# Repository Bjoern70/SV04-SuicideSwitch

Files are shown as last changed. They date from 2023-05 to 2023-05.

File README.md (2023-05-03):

# SUICIDE SWITCH FOR SOVOL SV04 IDEX 3D-PRINTER

## Specification:

### Requirements:

 - Add functionality to power off SV04 printer automatically after finishing print.
 - Safe electrical relization with minimum changes on existing high voltage connections.
 - Low power consumption of additional electronic components iot ensure motherboard / printer stability.
 - Maximum cost below 50 EUR / US-$

### Hardware approach:

 - Use solid state relais (SSR) to switch high voltage phase connection of power supply unit (PSU).
 - Avoid separate high voltage switching outside of SSR. Use low power push-button & separate 9V battery instead.
 - Build separate power-on panel to start printer. Use LEDs to visualize when SSR is powered by Battery and/or PSU.
 - Fix power-on panel to printer structure outside of printer cabinet.
 - Minimize number of & electronic components inside power-on panel.
 - Electronic components inside cabinet have to be fixed casing without impact on cooling & minimum impact on existing components.
 - Use 24V DC to power SSR when printer has started. Limit current to minimize power consumption & SSR input.
 - Use darlington transistor to minimize current consumption from J2 connector.

### Software approach:
 - Utilize spare J2 connector on v5.2.1 motherboard as suicide pin:
 - Add pin definition to motherboard "pins_CREALITY_V4.h" / "pins_CREALITY_V521.h" file: 
  ```//
  // SuicidePin
  //
  #define SUICIDE_PIN PE4 // Connector J2
  #ifndef SUICIDE_PIN_STATE
    	#define SUICIDE_PIN_STATE LOW
  #endif
  Reconfigure Marlin firmware "configuration.h" file iot use M81 g-code command (Power Off):
  // Custom Power Supply Control
  //
  #define HAS_SUICIDE_PIN
  //
  ```
- Add enable/disable auto power-off function to print options display screen.
- Add global bool variable to file "LCD_RTS.h" representing auto power-off enabled/disabled state. Add icons representing state to file "41_control.icl".
- Add AUTO_POWER_OFF_ICON_VP address definition to file "LCD_RTS.h". Add menu item to change state to adjustment phase in 32_main.icl.
- Add handling routine for state change to file "LCD_RTS.cpp" Add state check to suicide() function in MarlinCore implementation.
 
# Operating instructions:

## Power on printer:

- Switch on printer power switch => printer stays powered off. 

- Press push button on panel => yellow LED lights up. 

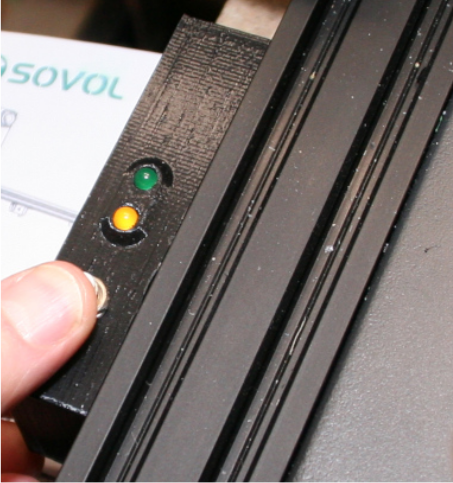
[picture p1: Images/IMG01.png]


- Hold button until green LED lights up.

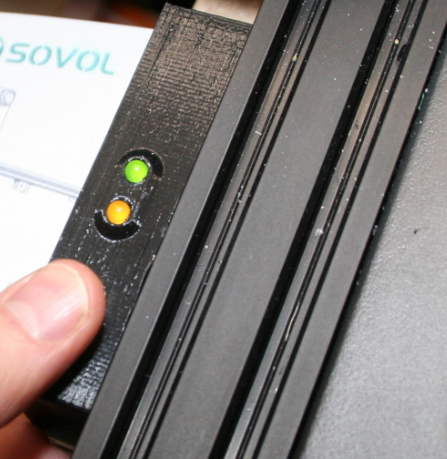
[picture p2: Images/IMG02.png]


- Release button => printer stays powered on.

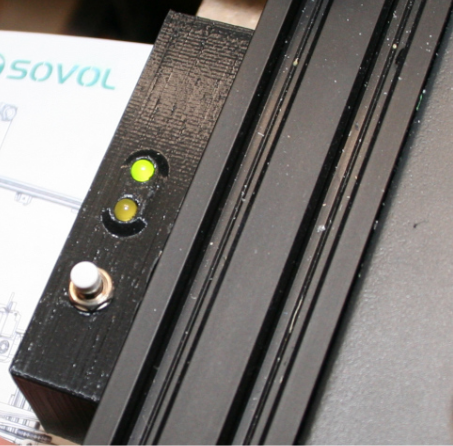
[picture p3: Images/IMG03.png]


## Turn off printer: 

- Option A: Use power switch to turn off.

- Option B: Use power off function in settings menu.

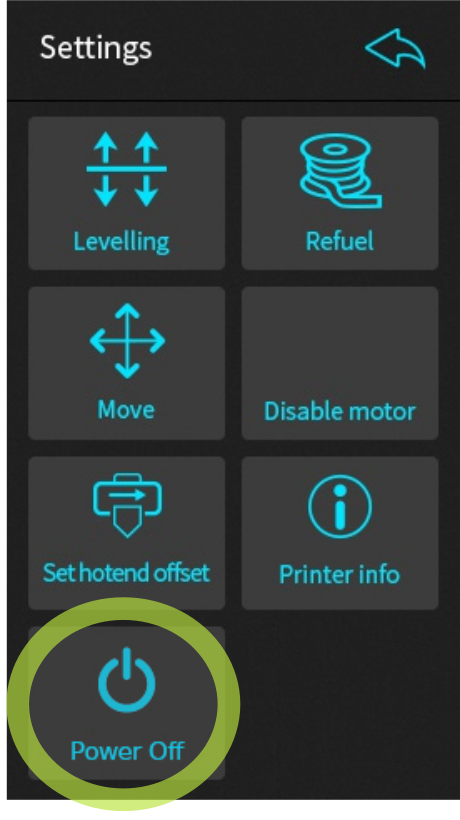
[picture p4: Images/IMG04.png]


- Option C: Add M81 gcode command to custom slicer end gcode. Printer will turn off when executing this instruction. 
   ```
   ; Example for prusa-slicer:
   ; nozzle cool-down & power off command
   M84 ; disable motors
   M104 S0 T0 ; turn off nozzle 0 temperature
   M104 S0 T1 ; turn off nozzle 1 temperature
   M140 S0 ; turn off bed
   M106 P0 ; fan max power iot prevent dropping of filament
   M109 S90 T0 ; wait for nozzle 0 cooldown
   M109 S90 T1 ; wait for nozzle 1 cooldown
   M81 ; suicide
   ```
# Build instructions:

## Important note: 	Changing your printer hardware might void your warranty. Follow this instructions on your own risk & liability.

## List of parts (maybe some components seem over-powered, but I had them available):
- solid state relais type SSR DA-20 
- NPN darlington transistor BDX53C
- Mini push button 0.3A, normally open, 7.2mm (9/32") mounting hole
- LED green, 5mm, 20mA
- LED yellow, 5mm, 20mA
- resistor 10KΩ, 0.25W
- resistor 1KΩ, 0.25W
- resistor 470Ω, 0.25W
- 9V block battery
- 9V battery snap
- cable grommet, 6mm diameter
- 10-20x cable zip tie
- 2x forked cable lug, 1.5-2.5mm², hole diameter M5
- 2m wire yellow+brown+red
- heat shrink tube 4mm diameter
- JST XH 2.54 3-Pin female connector
- 2x socket / button head screw M4x20mm + hex nut
- flat / countersunk screw M3x8mm + washer + hex nut
- 4x socket cap head screw M4x20mm + M4 T-slot nut

## Optional parts to support inside cabinet installation:
- SV04_Side_Supports.stl derived from: https://www.thingiverse.com/thing:5674611
- 3x socket / button head screw M4x10mm + washer + M4 T-slot nut

## Circuit diagram:

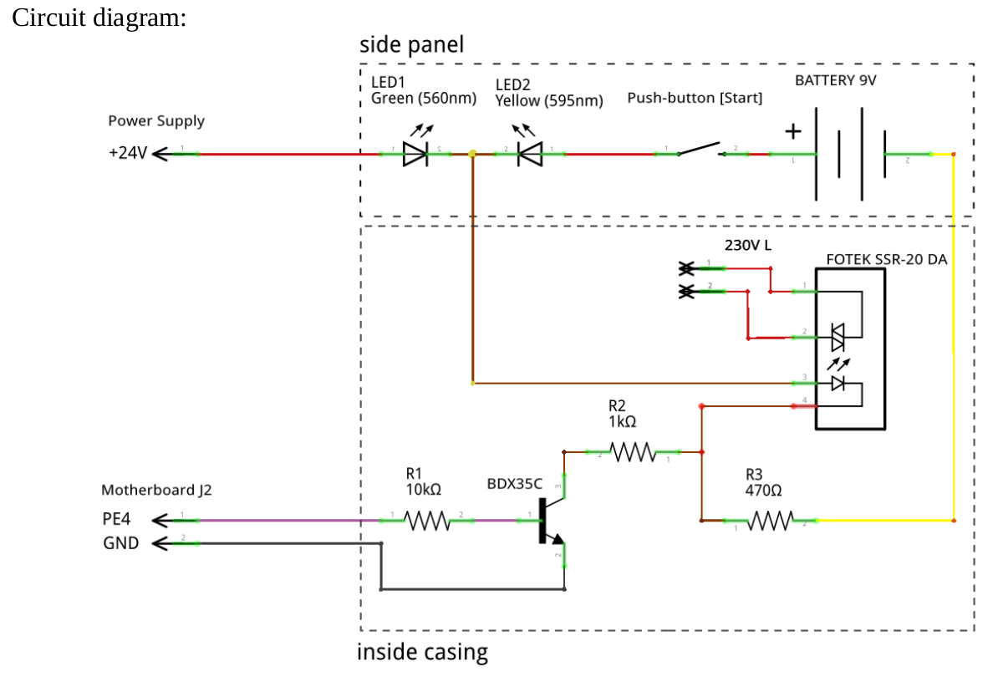
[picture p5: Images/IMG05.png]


## Build side panel:
- Print side panel file "SidePanel.stl".
- Minimum cable length is 60cm/24inch. 3 wires (red, brown, yellow) are needed. 
- Insert yellow LED next to push button opening. Insert green LED. Ensure that LED cathodes point to each other. Bend, cut & solder both LED cathodes with brown cable.
- Bend, cut & solder green LED anode with red cable. Use shrink tube to insulate.
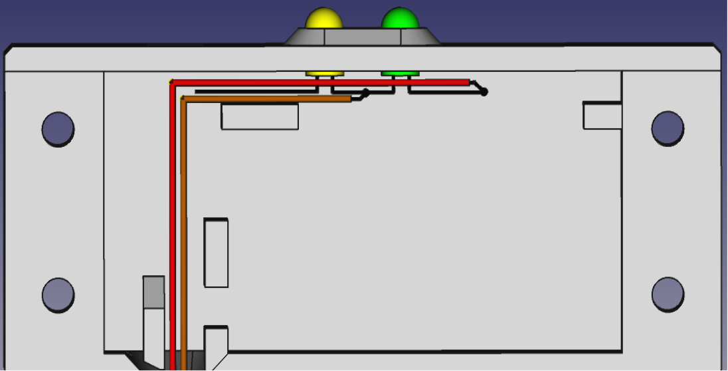
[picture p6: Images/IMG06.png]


- Insert & fasten mini push button. Bend, cut & solder yellow LED anode with mini push button contact. Attach other mini push button contact to positive/red battery snap wire & solder. 
- Connect negative/black battery snap wire to yellow cable & solder. Use shrink tube to insulate.
- Add cable tie for strain relief or just wrap cable around post as pictured. 
- Attach 9V battery to battery snap & insert into side panel. 
- Insert four M4x20mm screws & attach M4 T-slot nuts.

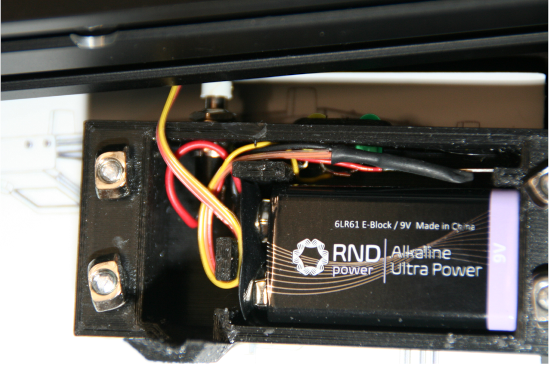
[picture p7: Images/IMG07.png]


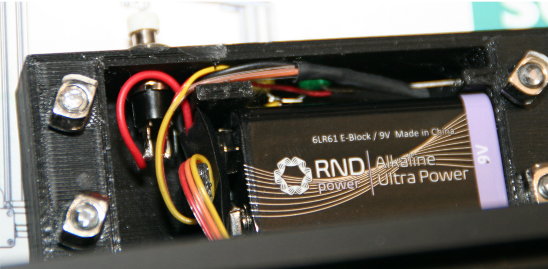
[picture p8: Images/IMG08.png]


## Cabinet preparation:

### IMPORTANT SAFETY NOTE: Unplug power cord first.
- Mark SSR drill holes on top of the cabinet.

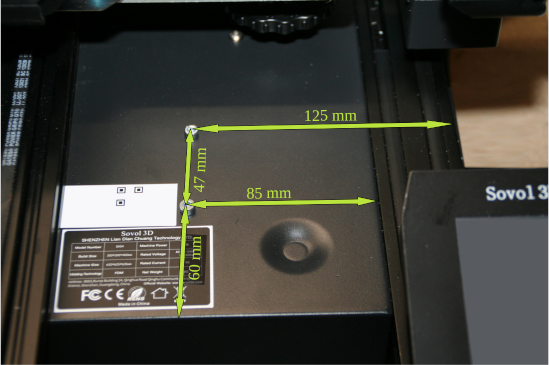
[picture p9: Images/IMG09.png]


- Install optional side supports, lay down printer on its right side.

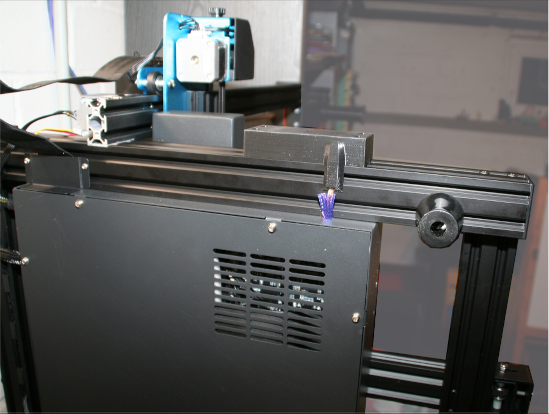
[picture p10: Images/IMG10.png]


- Remove bottom plate screws.
- Cover inside of drilling area with a strip of duct tape iot catch all metal drilling chips & a piece of wooden board iot avoid damage to motherboard / ribbon cable in case of accidently drilling too deep. Carefully drill 6mm hole into left side of cabinet.

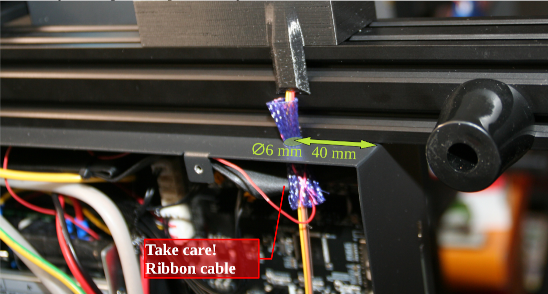
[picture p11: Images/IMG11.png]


- Cover inside of drilling area with a strip of duct tape iot catch all metal drilling chips. Carefully drill two 4,5 mm SSR holes into top side of cabinet. Ensure that holes match SSR fasteners & that sufficent space is left to mount & connect the SSR.

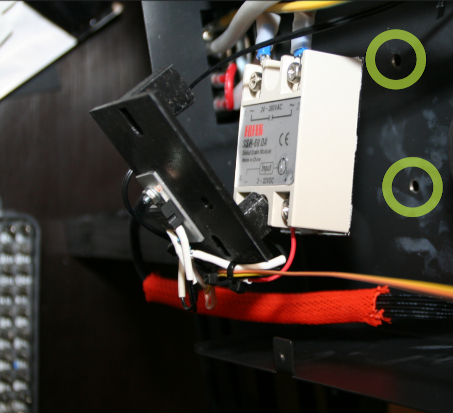
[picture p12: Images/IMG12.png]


- Insert cable grommet into 6mm hole. Mount side panel, pull side panel cable through cable grommet.

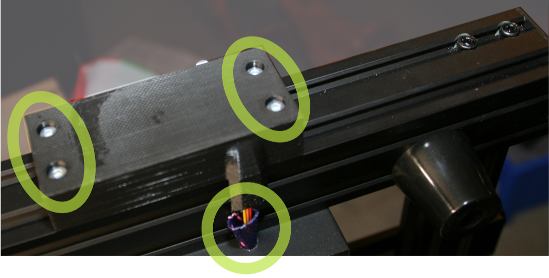
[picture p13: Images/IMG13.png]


- Prepare mainboard JST connector:
- Minimum cable length is 40cm/16inch. Only 2 wires (PE4 + GND) are needed. 

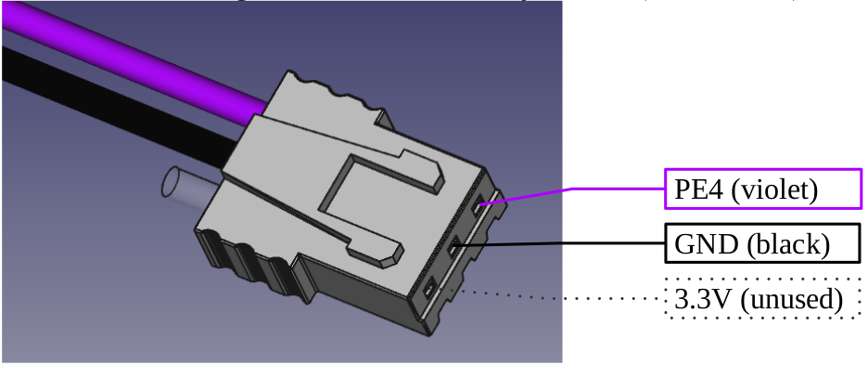
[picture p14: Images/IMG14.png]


##Build inside cabinet unit:
- This design does not use a circuit board. All electronic parts will be attached to the SSR/SSR cover. 
- Print SSR cover file "SSR_cover.stl".
- Insert M3x8mm screw into countersunk hole.

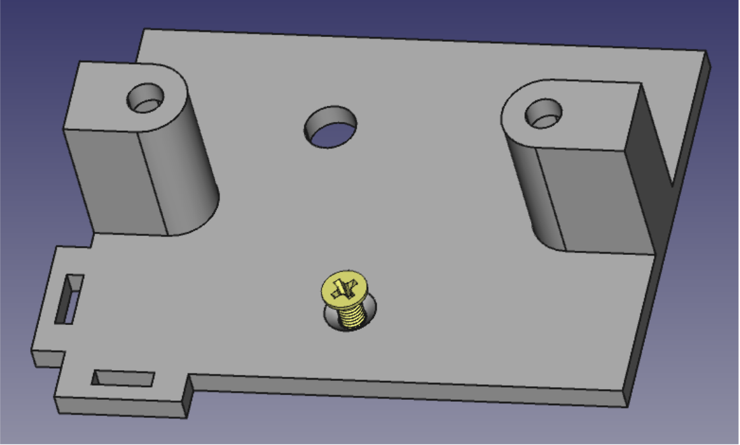
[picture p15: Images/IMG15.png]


- Fix transistor (& optional cooling plate) to M3x8 screw using hex nut & washer.

- Put 40mm shrink tube on JST connector violet cable (PE4). Cut & solder 10KΩ resistor to transistor base (bottom pin). Cut & solder other resistor end to JST connector violet cable (PE4). Shrink tube to insulate transistor pin & resistor.
- Cut & solder 1KΩ resistor to transistor collector (middle pin). Cut & solder other 1KΩ resistor end to 470Ω resistor & 10cm red wire (will be attached to SSR terminal 4). Put 40mm shrink tube on yellow side panel cable. Cut & solder other 470Ω resistor end to yellow side panel cable. Shrink tube to insulate 470Ω resistor.
- Use shrink tube to insulate red SSR wire next to 1KΩ resistor. Fasten red SSR wire to SSR terminal 4 (-).
- Put 40mm shrink tube on JST connector black cable (GND). Cut & solder transistor base (top pin) to JST connector black cable (GND). Shrink tube to insulate transistor pin & cable.
- Fasten brown side panel cable wire to SSR terminal 3 (+).

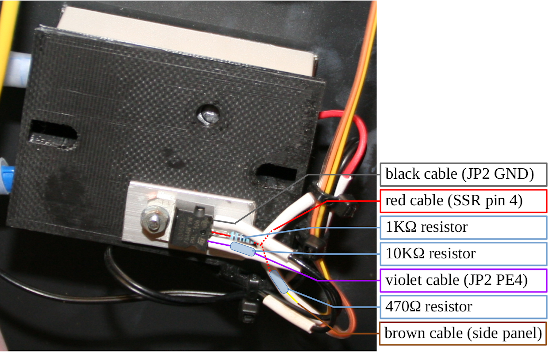
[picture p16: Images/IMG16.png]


- Place SSR & insert M4x20mm screws into cabinet holes & SSR mounts. Remove mounted cable ties if necessary. Attach cutting mark onto red power cable from power inlet. Ensure to have sufficent cable length to mount both power cable ends to SSR connectors 1 & 2.
- Cut red power cable at cutting mark, strip a bit of insulation & use crimping tool to attach fork cable lugs to power cable ends. Attach power cable from power inlet to SSR terminal 1. Attach power cable from power supply unit to SSR terminal 2.
- Ensure that all SSR connectors are fixed firmly. 
### Note: All pictured power cables were shielded with extra silicone tubes.

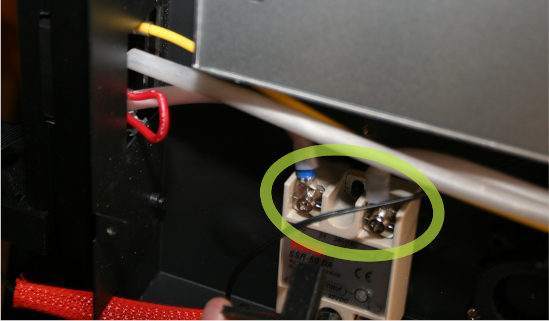
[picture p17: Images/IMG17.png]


- Insert M4 nuts into SSR shield. Fasten M4x20mm screws through cabinet top side holes. Ensure that screws are tight.

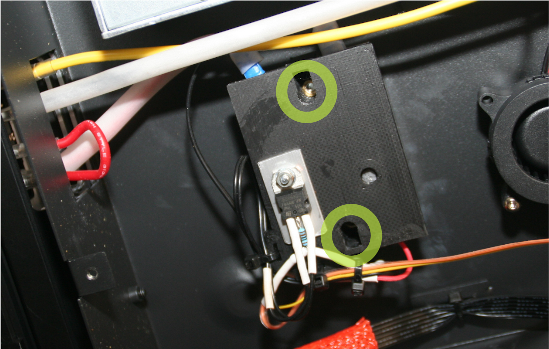
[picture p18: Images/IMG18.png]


- Strip 20mm of side panel red cable end. Form a loop with 5mm diameter & solder it. Remove power supply unit terminal cover. Attach loop to power supply unit "+V" terminal. Ensure that terminal screw is tight. Fix power supply unit terminal cover.

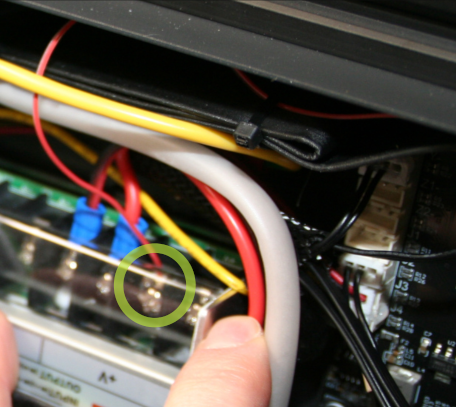
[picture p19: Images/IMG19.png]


## Test installation:
- The power cord stays disconnected. Use multimeter to check resistance between power inlet & power supply unit "L" terminal. Resistance diplayed should be very high (between xxx MΩ and infinite). 
- Press & hold push button. Ensure yellow LED lights up. Ensure SSR LED lights up, too. Ensure resistance displayed is low (between 0 and xx Ω).
- Unscrew side panel.  Use multimeter to check resistance between 9 V battery negative-terminal and transistor housing. Resistance diplayed should be 1470 Ω +/- 10% resistor tolerance.
- Use multimeter to check resistance between JST connector PE4 pin and GND pin. Resistance diplayed should be higher than 20 KΩ.

## Final hardware installation:
- Plug JST connector into port J2 on motherboard

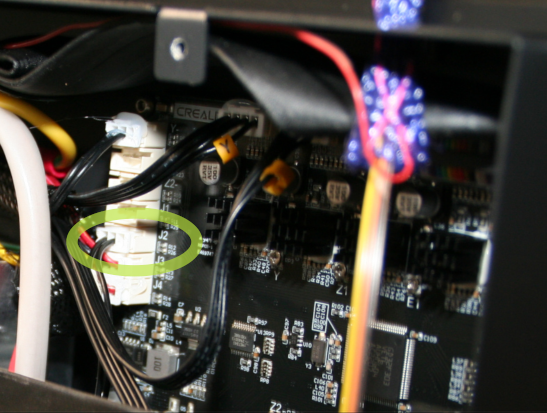
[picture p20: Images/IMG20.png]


- Reinstall all removed cable ties. Firmly fix all resistors & SSR wires to SSR cover with cable ties. Fix all other addional wires with cable ties.
- Fix bottom plate by installing all 8 screws. Connect power cord.
- Power on printer as described in operating instructions above.

# Software installation:
- Use SDcard to install printer firmware that supports power-off functionality from  https://github.com/Bjoern70/SV04-IDEX-3D-Printer-Mainboard-Source-code/releases
- Turn printer off & remove display backcover. Use microSD card to install display software that supports power-off functionality from https://github.com/Bjoern70/SV04-Touchscreen/releases
- Install display backcover.
- Change custom end gcode settings in your slicer profiles iot to power-off printer after printing process by default.
### Enjoy your new printer features!

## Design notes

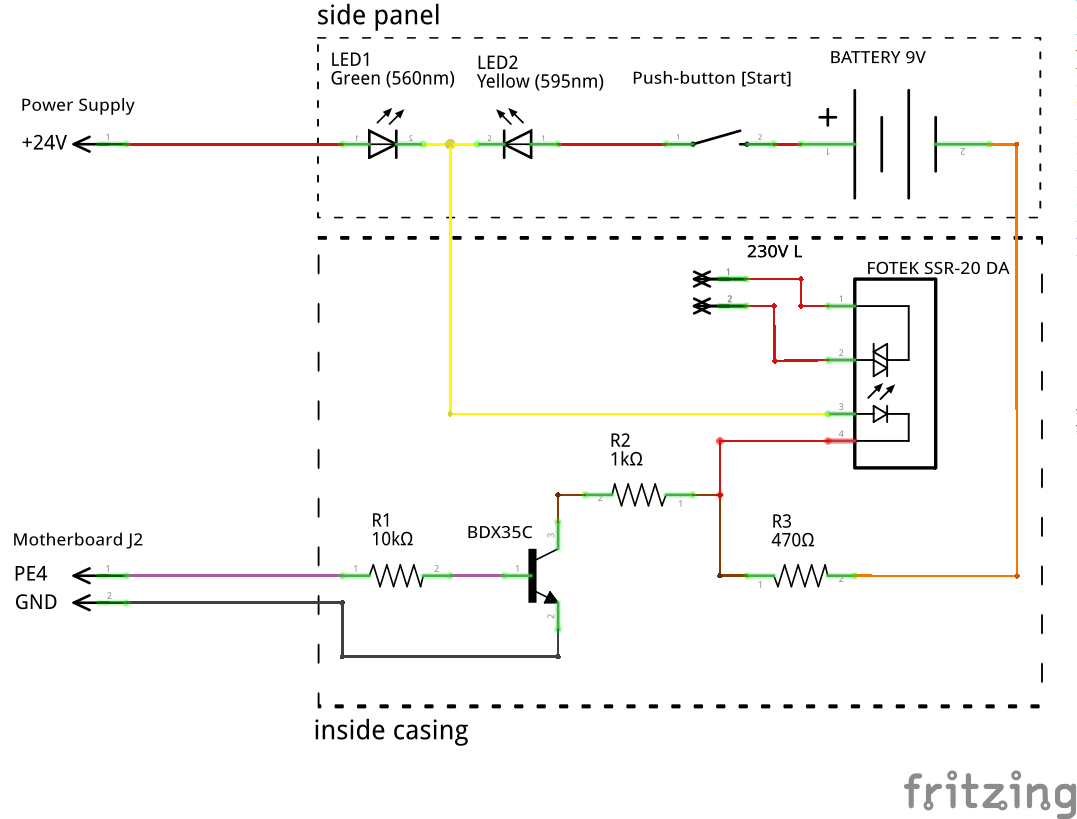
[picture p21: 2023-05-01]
SuicideSwitch cuircuit.png

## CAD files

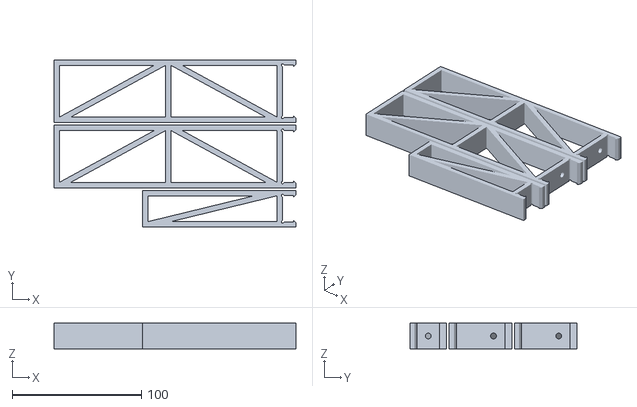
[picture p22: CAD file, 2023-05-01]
SV04_Side_Supports.stl
187.0 x 129.2 x 20.0

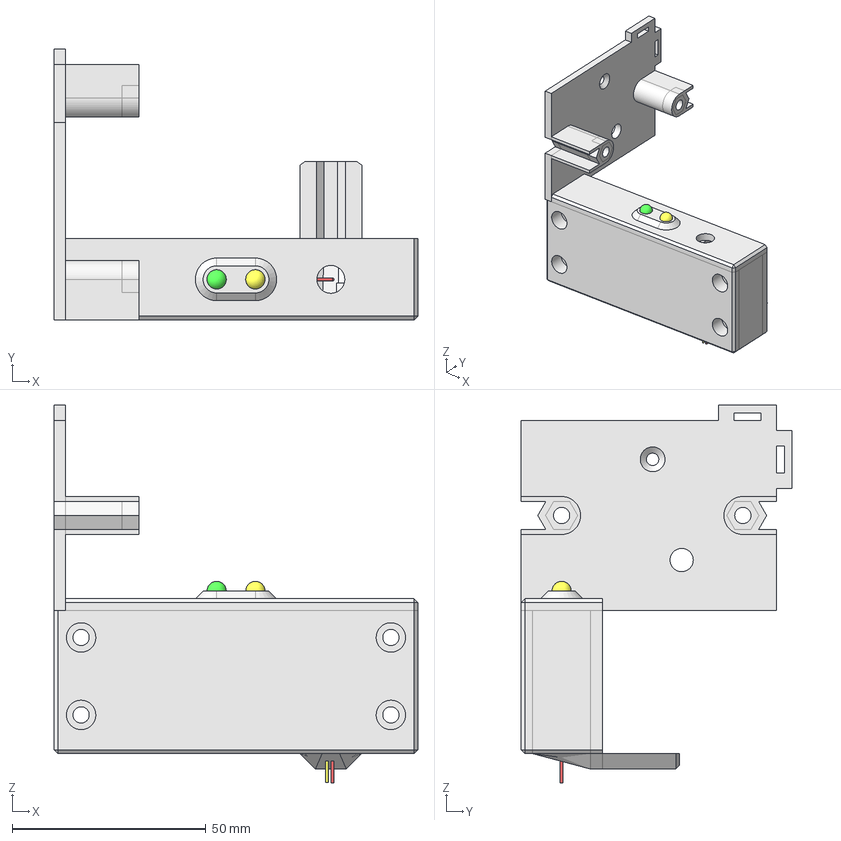
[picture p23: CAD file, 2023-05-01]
SSR_Cover+SidePanel.FCStd
94.0 x 70.0 x 97.5 mm
Panel
SSR_Cover
Zylinder005
Kugel
Kugel001
Zylinder006
Zylinder007
Zylinder008
Zylinder009
Zylinder010
Zylinder011
Zylinder012
Zylinder013
Kugel002
Zylinder014
Kugel003
Zylinder015
Zylinder017
Kugel004
Zylinder018
Kugel005
Zylinder019
Kugel006
Zylinder020
Zylinder021
Zylinder022
Kugel007

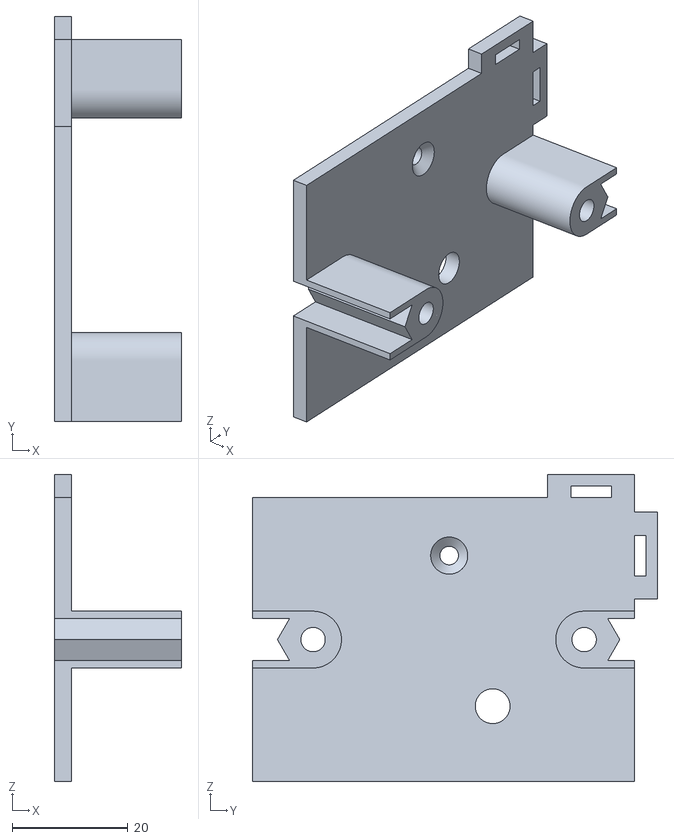
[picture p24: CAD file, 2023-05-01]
SSR_Cover.stl
22.0 x 70.0 x 53.0

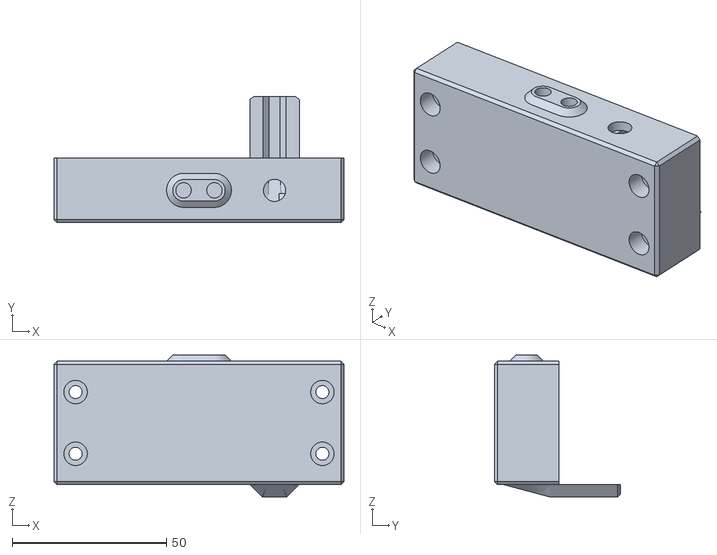
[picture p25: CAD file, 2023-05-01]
SidePanel.stl
94.0 x 41.0 x 46.0
